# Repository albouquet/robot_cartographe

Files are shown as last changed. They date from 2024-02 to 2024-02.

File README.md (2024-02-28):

# Projet : Robot cartographe
## Par Alexandre Bouquet

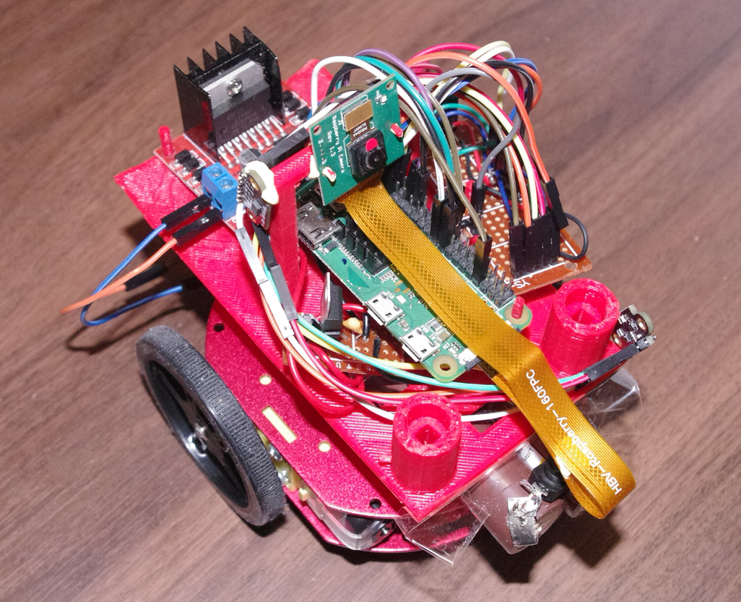
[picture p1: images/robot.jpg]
Robot Cartographe


## Introduction

L’objectif du projet est de créer un robot récupérant des informations télémétriques sur son environnement, afin d’en réaliser un mappage 2D de ce dernier.

Grâce à une connexion WIFI, le robot doit pouvoir envoyer un flux vidéo à l’utilisateur, recevoir les commandes de navigation de celui-ci, et transmettre des données télémétriques (+ coordonnées x,y du robot).

A coté de cela, un logiciel devra réaliser le plan 2D de l’environnement du robot, grâce aux données reçues.

## Partie I : Choix des composants

Je suis partie d’un support comportant deux motoréducteurs, deux roues et une bille centrale.

J’ai choisi une Raspberry pi zéro pour le contrôle central, pour plusieurs raisons :
* Développement rapide avec python
* Déjà équipée d’une caméra, du wifi et de GPIO
* De petite taille, faible consommation

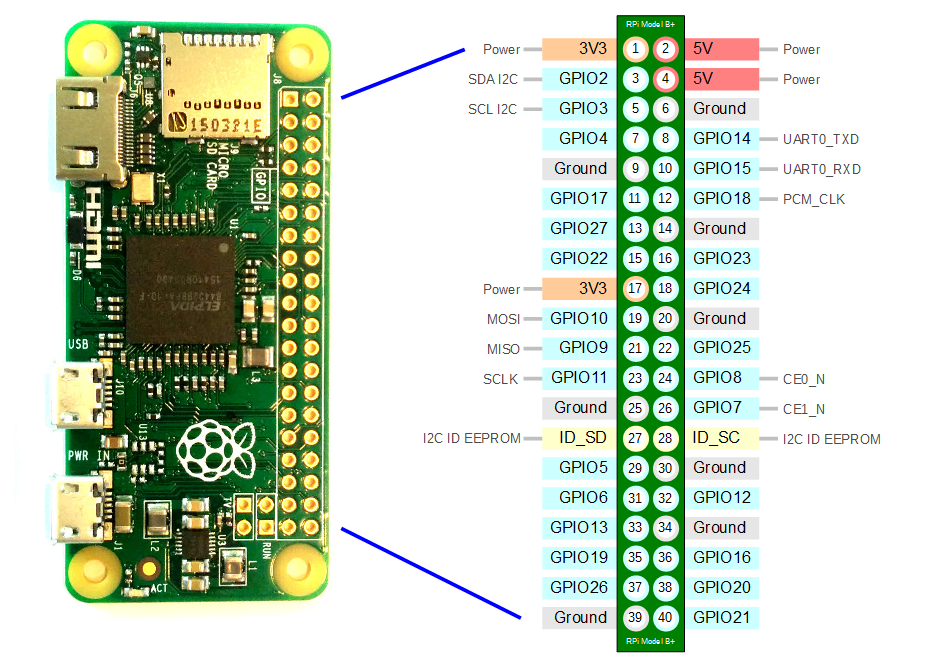
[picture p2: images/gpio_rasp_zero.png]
Figure 1: Raspberry pi zero


Deux capteurs télémétriques VL53L0X sont utilisés. La distance mesurée est de l’ordre du mètre.
En effet, ne sachant pas exactement la structure finale du projet, je suis finalement resté sur ce modèle.

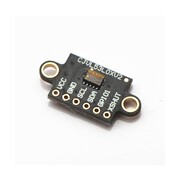
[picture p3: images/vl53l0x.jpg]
Figure 2: Capteur VL53L0X


Afin de contrôler les deux moteurs, j’utilise le L298N. Doté d’un pont en H et d’un régulateur 5v, il permet de piloter les moteurs d’avant en arrière pour chacun d’eux, grâce à des signaux PWM et de contrôles.

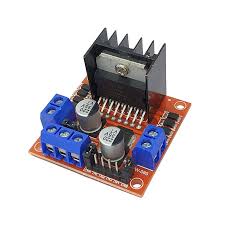
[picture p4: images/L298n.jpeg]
Figure 3: Module L298N


Deux batteries 18650 (pour un total de 8,4v) permettent d’alimenter la Raspberry pi et le L298N.

## Partie II : Alimentation

Comme dit précédemment, le L298N possède une sortie 5V. Je pensais l’utiliser pour alimenter la Pi lorsque je me suis rendu compte qu’elle pouvait délivrer moins de 500mA. 
Or, le démarrage de la Raspberry pi est consommateur. 
De plus, l’alimentation est bruitée lorsque les moteurs sont utilisés.

J’ai donc décidé de créer une alimentation stabilisée de 5V, alimentée par les batteries.
Pour cela, j’ai utilisé le régulateur 5V L7805CV, combiné avec deux condensateurs afin de filtrer la sortie.

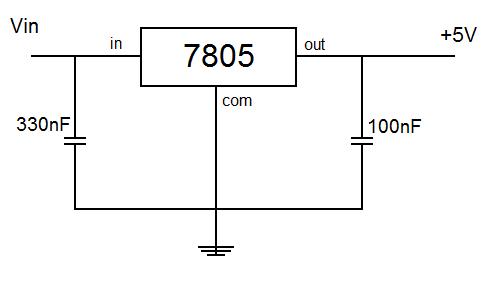
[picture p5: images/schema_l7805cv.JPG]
Figure 4: Schéma aliementation régulée à 5V


L’ensemble est soudé sur une carte à pastille :

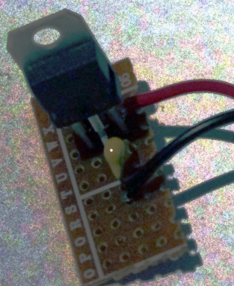
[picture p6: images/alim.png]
Figure 5: Régulateur 5V soudé sur plaque à pastille


## Partie III : Contrôle des Moteurs

Le L298N permet le contrôle de 2 moteurs grâce à :
* 2 signaux PWM pour l’alimentation
* 4 signaux de contrôles pour le sens de rotation

Ce module est directement alimenté par les batteries. La Raspberry pi fournie les 6 signaux nécessaires pour l’utilisation du module grâce à ses GPIO.

La tension moyenne nécessaire pour la rotation d’une roue est de 35 % de 8,4V donc environ 3V.

Les signaux PWM sont de type matériel sur la Pi, ce qui évite de consommer du temps processeur pour les générer.

## Partie IV : Contrôle des capteurs

Les capteurs télémétriques utilisés sont les VL53L0X.
Ils communiquent à travers un bus I2C (SDA, SCL). Par défaut, les deux ont l’adresse 0x29 une fois connectés au bus.
Pour la changer (et pouvoir identifier les deux), j’utilise la broche XSHUT afin d’activer les capteurs un par un (et effectuer le changement d’adresse).

Pour relier les deux capteurs au bus I2C de la Raspberry Pi, j’ai soudé un bus sur une plaque à pastille, afin de mettre en commun l’alimentation, le SDA et le SCL :

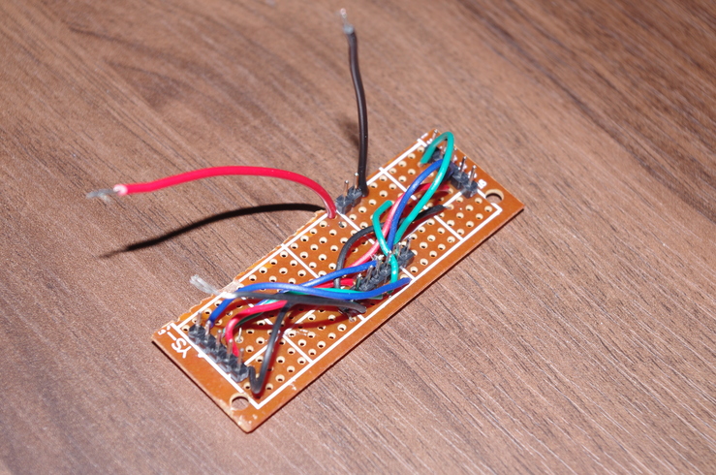
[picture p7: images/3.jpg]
Figure 6: Bus soudé pour relier les deux capteurs de distance au bus I2C


La bibliothèque python adafruit_vl53l0x permet un contrôle aisé des capteurs
(changement d’adresse + récupération distance).

Lorsque le capteur ne peut calculer la distance car celle-ci est trop grande (supérieur à 1.5 mètres), celui-ci renvoi 817 (plus de 8 mètres). C’est donc pris en compte lors de la réalisation du plan 2D.

## Partie V : Réalisation 3D

Afin de maintenir les composants en place sur le support, j’ai dessiné sous FreeCAD un deuxième support, et l’ai imprimé avec mon imprimante 3D :

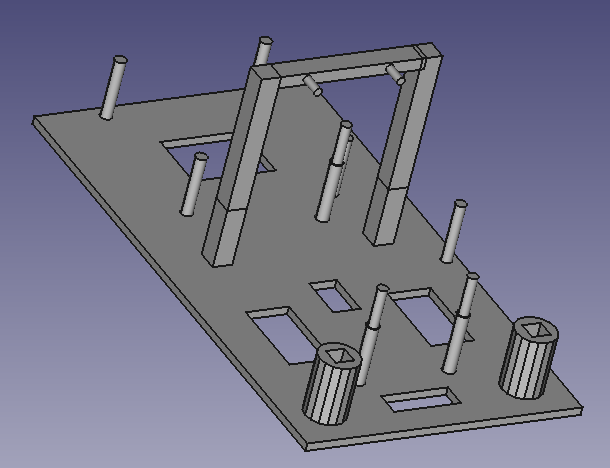
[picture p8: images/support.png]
Figure 6: Support


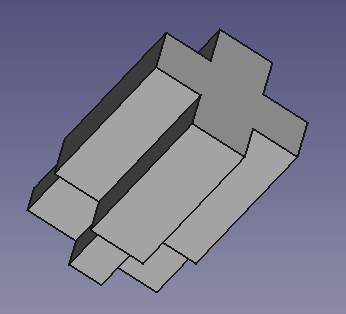
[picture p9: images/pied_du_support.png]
Figure 7: pied_Support

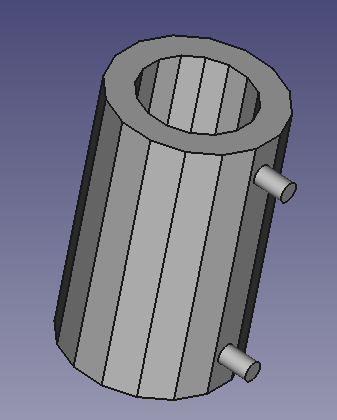
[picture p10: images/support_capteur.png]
Figure 8: Support_capteur


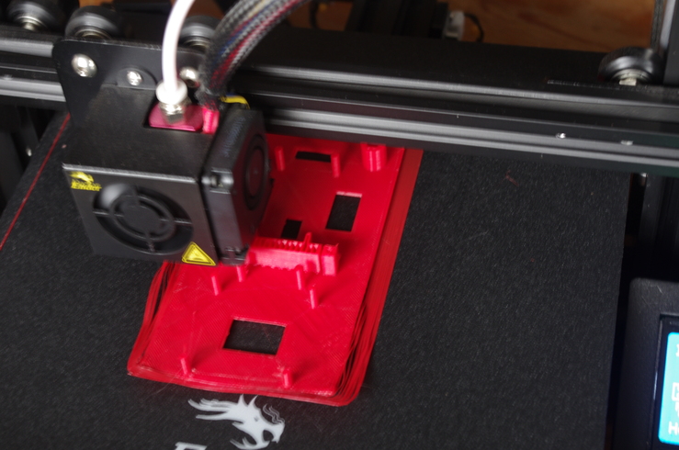
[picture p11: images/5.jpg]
Figure 9: Impre3D_1

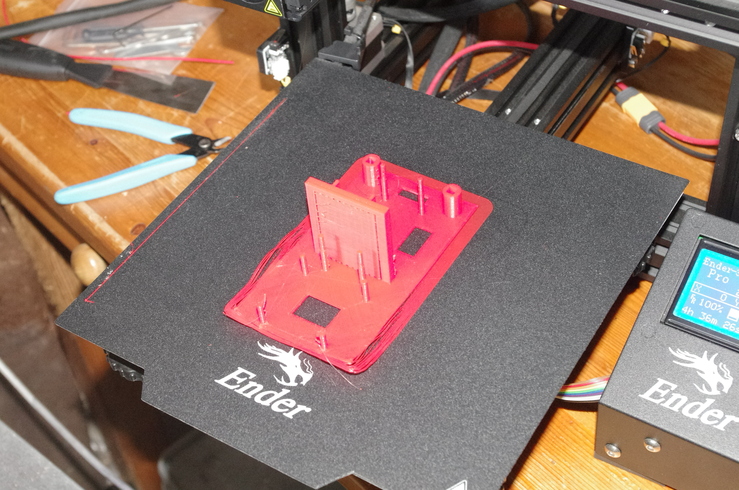
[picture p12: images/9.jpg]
Figure 10: Impre3D_2


## Partie VI : Fonctionnement du robot

Trois programmes python ont été réalisés : un pour la Raspberry pi (le robot), un pour l’ordinateur de l’utilisateur, un pour réaliser le mappage 2D avec le fichier de donnée.

Tout d’abord, la Raspberry pi se connecte à l’ordinateur de l’utilisateur.

Trois sockets sont utilisées :
* une pour l’envoi de la vidéo (type filelike)
* une pour l’envoie des données télémétriques et des coordonnées (x,y)
* une pour la réception des commandes de l’utilisateur

La vidéo et les données télémétriques sont stockées dans deux fichiers différents.

Si le robot effectue une rotation ou s’il avance, les coordonnées du robot (x et y) sont modifiées.

Par manque de temps, j’ai programmé des rotations de 90 degrés
uniquement. Cela simplifie les calculs de coordonnées du robot, et évite de
rajouter des erreurs de positionnement.

Lorsque le robot est en mode « avancer », les données des capteurs sont
transmises et les coordonnées s’adaptent toutes les 0,2 secondes.

Sur l’ordinateur de l’utilisateur, un terminal permet d’envoyer les
commandes, et récupérer la vidéo transmise par le robot, affichée grâce au
lecteur MPV.

La vidéo à un retard de plusieurs secondes par rapport à la réalité.
Le logiciel de mappage 2D dessine les liens entre tous les points renvoyés
par les capteurs. Il utilise la bibliothèque Matplotlib.

Schéma électrique final du projet :

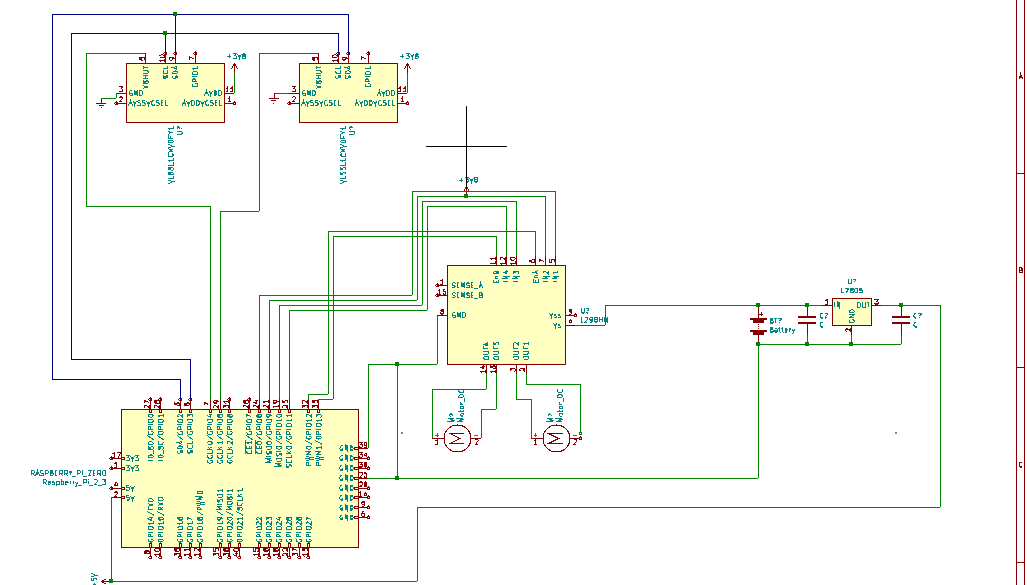
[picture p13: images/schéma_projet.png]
Figure 11: Schéma électrique du projet


## Partie VII : Tests

### Calibrage des capteurs VL53L0X

J’ai constaté que les capteurs ne renvoyaient pas la même valeur de distance pour une
même distance.

Par conséquent, j’ai réalisé une calibration des capteurs grâce à un plan fixe.
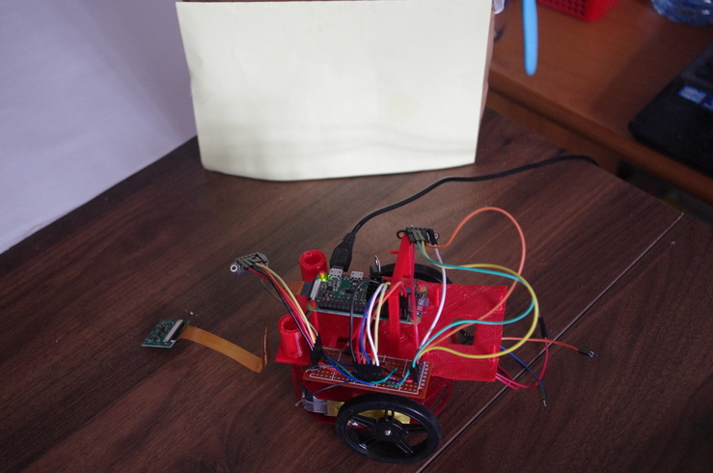
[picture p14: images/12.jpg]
Figure 12: Calibrage des capteurs de distance

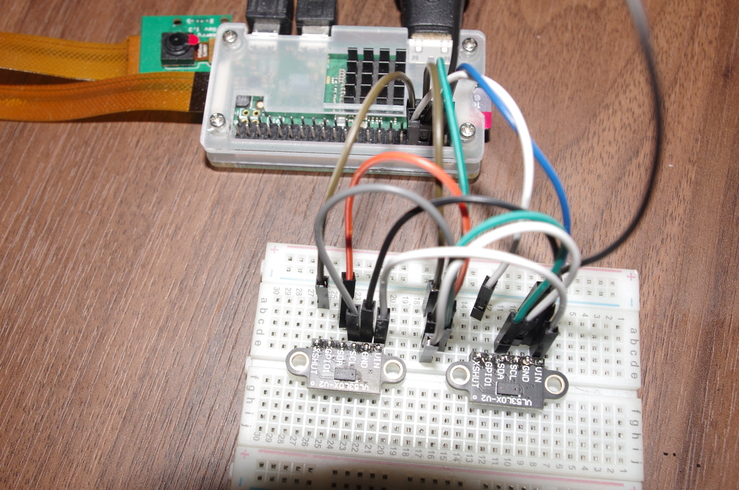
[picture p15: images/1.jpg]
Figure 13: Test capteurs de distance


### Vérification des signaux PWM pour les moteurs

Les signaux PWM sont générés par la Raspberry pi. Ils vont de 0 à 3.3V lorsque le
dutycycle est à 100 % :

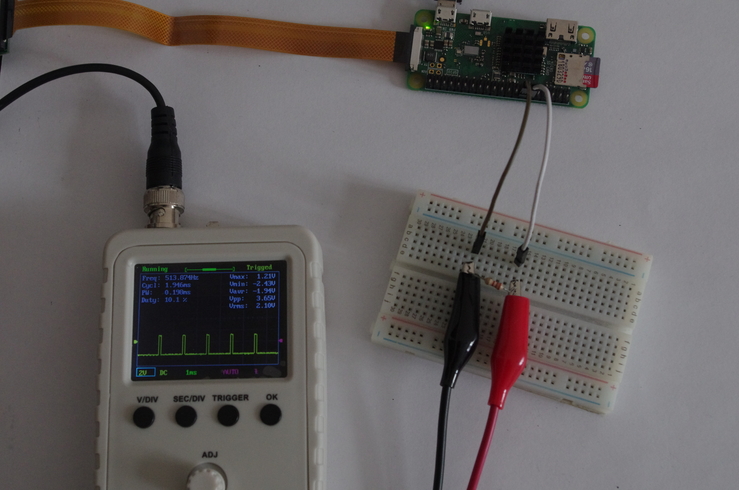
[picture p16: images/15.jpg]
Figure 14: Test PWM dutycycle à 10%


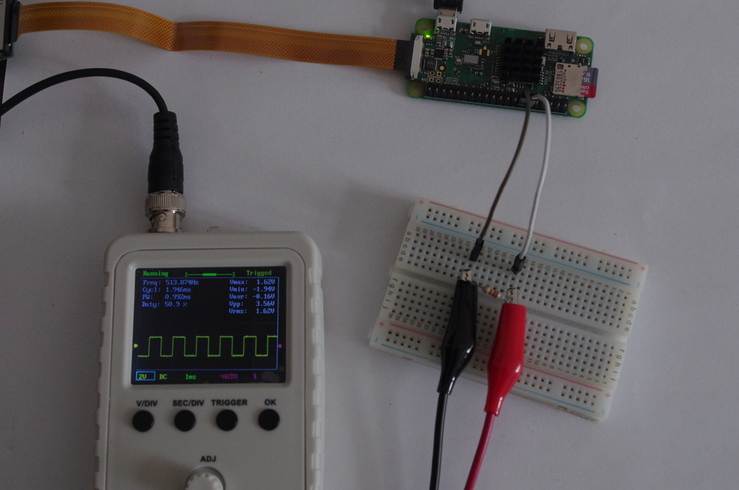
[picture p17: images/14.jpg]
Figure 15: Test PWM dutycycle à 50%


### Test complet du robot

J’ai réalisé le test de la totalité des fonctionnalités du robot sur une table plate.

Chacune a été testée :
* Connexion au réseau WIFI local
* Transmission/Réception des commandes de l’utilisateur
* Transmission/Réception du flux vidéo, données télémétrique, coordonnées du robot (x,y)
* Enregistrement dans un fichier la vidéo et dans un autre les données.
* Translation avant, rotation gauche/droite, arrêt

### Test sur parcours

J’ai vérifié la performance du robot sur un parcours intérieur, avec un sol avec des
rainures (sol non plat → voir la vidéo du projet). Le robot a réalisé les objectifs
attendus (transmission/réception vidéo, données, commandes).

Mais plusieurs problèmes ont été constatés :
* les roues du robot vibrent et ne permettent pas au robot de rester bien droit (perte de précision de positionnement du robot).
* L’engin en lui-même vibre beaucoup (désagréable sur la vidéo)
* Un sol qui n’est pas plat peut entraver le robot
* les rotations du robot sont très approximatives

Pour que le plan final soit parfait, il est nécessaire d’avoir les coordonnées de positon
du robot exacte et une fréquence d’envoi des données télémétriques assez grande.

VOIR video demo

### Modélisation 2D de l’environnement

Avec le programme réalisé nommé « mappage_2D », les coordonnées envoyées par
le robot ont pu être traitées afin de définir le plan de la zone d’évolution du robot :

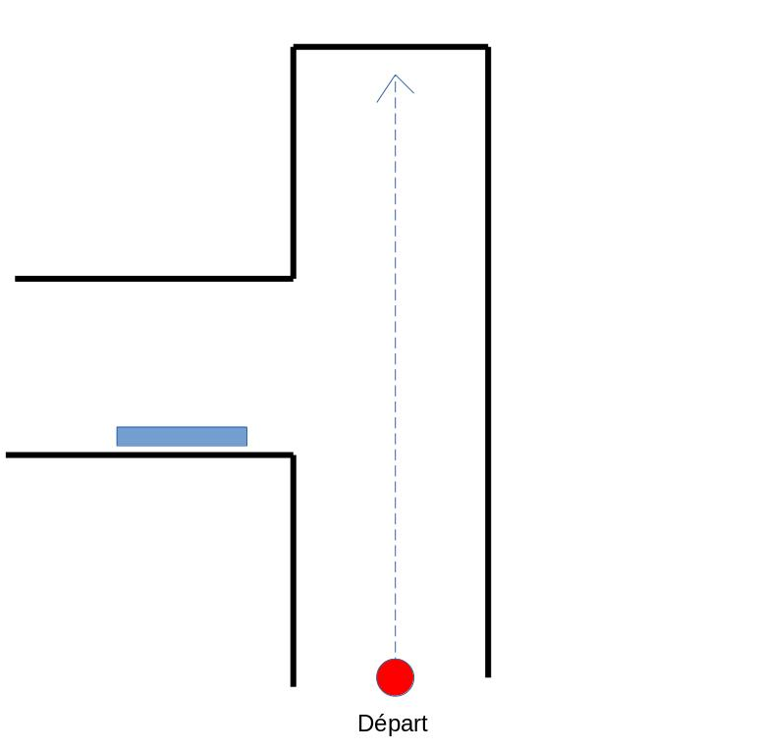
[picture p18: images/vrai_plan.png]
Figure 16: Vrai plan du terrain de test


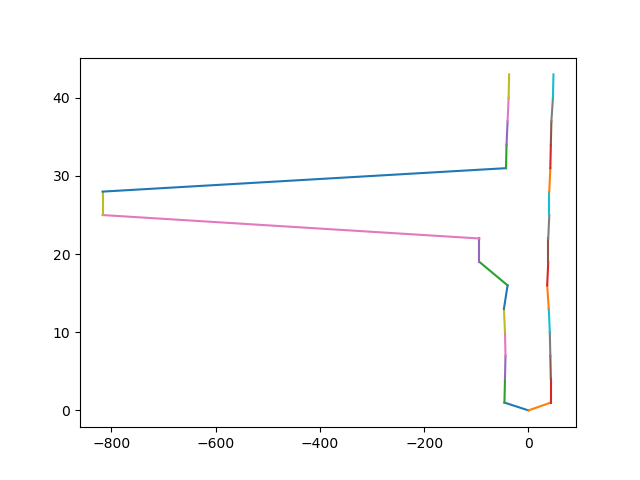
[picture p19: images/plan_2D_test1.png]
Figure 17: Plan 2D créé par le robot (conservation des points de vide)


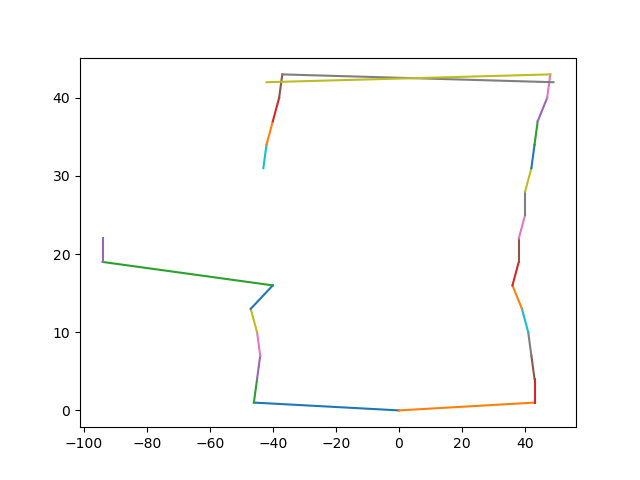
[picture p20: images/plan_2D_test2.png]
Figure 18: Plan 2D créé par le robot (sans point de vide)


## Partie VIII : Points d’améliorations

La structure du robot doit être améliorée afin d’éviter tout basculement et vibration
du robot.
De plus, la façon de calculer la position du robot (en fonction de la rotation et du temps de translation) est à changer par une technique plus précise.
Enfin, je n’ai pas eu le temps de réaliser le traitement des images reçues pour augmenter la précision de la modélisation de l’environnement.

## Conclusion
Ce projet a demandé des compétences dans différents domaine, comme la programmation python, le réseau, Linux, l’électronique et la CAO.

Le prototype du robot cartographe réalise les objectifs attendus :
* Réception des commandes
* Transmission vidéo, données télémétrique
* Mappage 2D proche du plan réel du terrain

Mais il comporte un certains nombres de points à améliorer, de la structure non fixe, à la précision du mappage 2D, en passant par la maîtrise de l’angle de rotation de l’engin.

### A savoir

Le programme à placer sur la Raspberry pi est prog_pi.py

Le programme à placer sur l'ordinateur de l'utilisateur est prog_utilisateur.py

Le programme pour mapper un plan 2D gràce à un fichier de données est mappage_2D.py

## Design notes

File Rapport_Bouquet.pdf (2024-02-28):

# Projet Robot cartographe

### Alexandre Bouquet

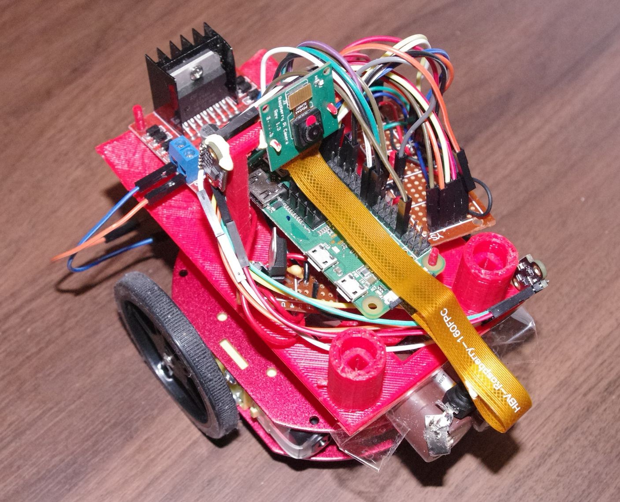
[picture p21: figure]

Sommaire

## Introduction

L’objectif du projet est de créer un robot récupérant des informations télémétriques sur son environnement, afin d’en réaliser un mappage 2D de ce dernier.
Grâce à une connexion WIFI, le robot doit pouvoir envoyer un flux vidéo à l’utilisateur, recevoir les commandes de navigation de celui-ci, et transmettre des données télémétriques (+ coordonnées x,y du robot).
A coté de cela, un logiciel devra réaliser le plan 2D de l’environnement du robot, grâce aux données reçues.

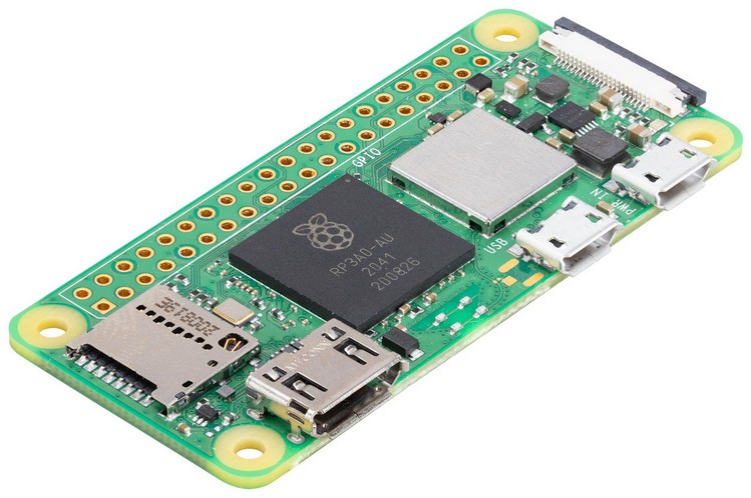
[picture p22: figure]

Figure 1: Raspberry pi zero

## Partie I : Choix des composants

Je suis partie d’un support comportant deux motoréducteurs, deux roues et une bille centrale.

J’ai choisi une Raspberry pi zéro pour le contrôle central, pour plusieurs raisons :
- Développement rapide avec python
- Déjà équipée d’une caméra, du wifi et de GPIO
- De petite taille, faible consommation

Deux capteurs télémétriques VL53L0X sont utilisés. La distance mesurée est de l’ordre du mètre. En effet, ne sachant pas exactement la structure finale du projet, je suis finalement resté sur ce modèle.

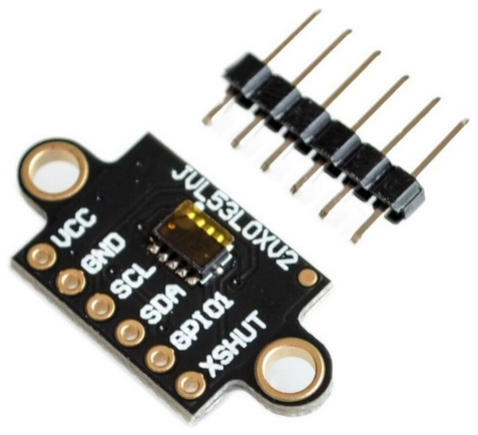
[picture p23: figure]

Afin de contrôler les deux moteurs, j’utilise le L298N. Doté d’un pont en H et d’un régulateur 5v, il permet de piloter les moteurs d’avant en arrière pour chacun d’eux, grâce à des signaux PWM et de contrôles.

Deux batteries 18650 (pour un total de 8,4v) permettent d’alimenter la Raspberry pi et le L298N.

Figure 2: Capteur VL53L0X

Figure 3: Module L298N

## Partie II : Alimentation

Comme dit précédemment, le L298N possède une sortie 5V. Je pensais l’utiliser pour alimenter la Pi lorsque je me suis rendu compte qu’elle pouvait délivrer moins de 500 mA. Or, le démarrage de la Raspberry pi est consommateur. De plus, l’alimentation est bruitée lorsque les moteurs sont utilisés.
J’ai donc décidé de créer une alimentation stabilisée de 5V, alimentée par les batteries. Pour cela, j’ai utilisé le régulateur 5V L7805CV, combiné avec deux condensateurs afin de filtrer la sortie.

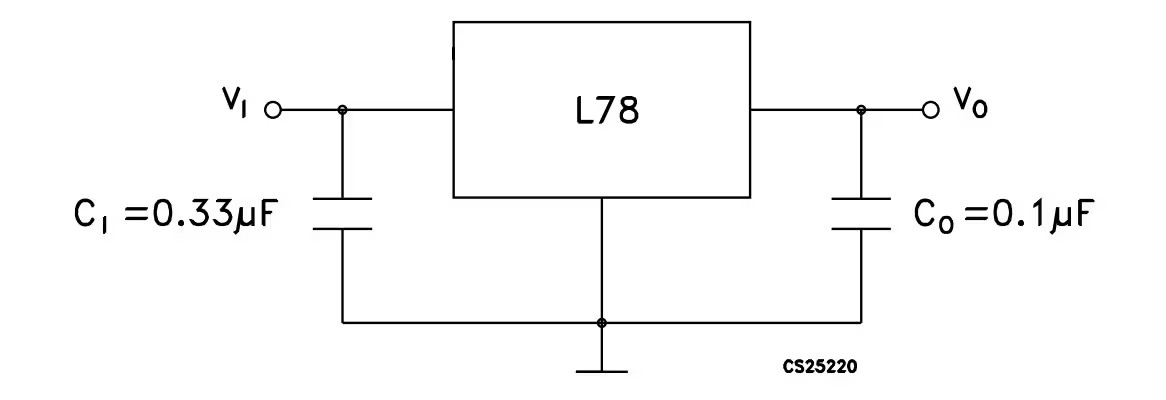
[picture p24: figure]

L’ensemble est soudé sur une carte à pastille :

Figure 4: Schéma aliementation régulée à 5V

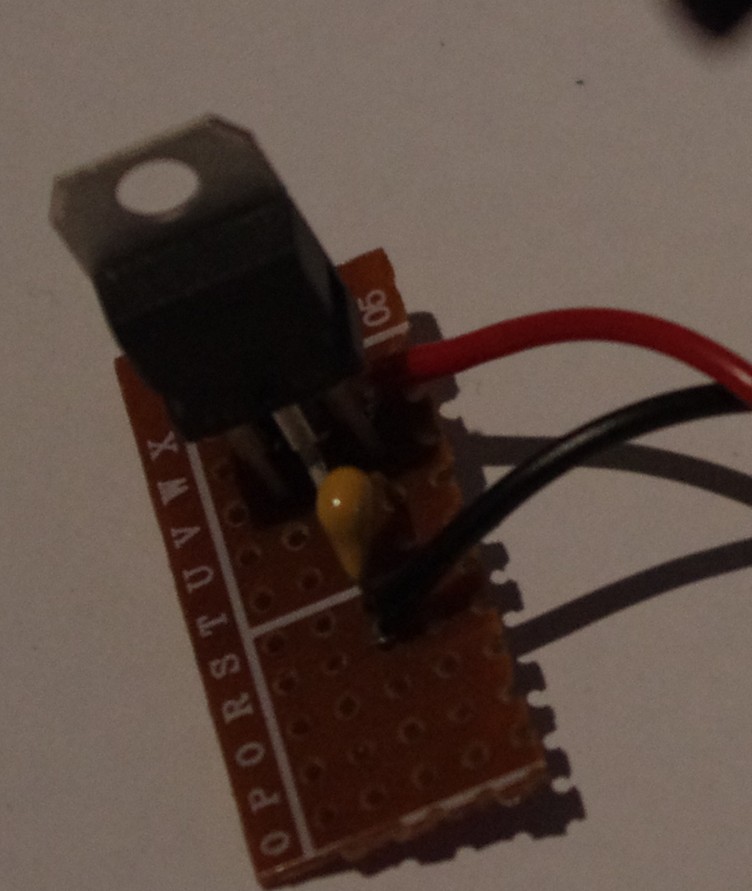
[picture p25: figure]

Figure 5: Régulateur 5V soudé sur plaque à pastille

## Partie III : Contrôle des Moteurs

Le L298N permet le contrôle de 2 moteurs grâce à :
- 2 signaux PWM pour l’alimentation
- 4 signaux de contrôles pour le sens de rotation

Ce module est directement alimenté par les batteries. La Raspberry pi fournie les 6 signaux nécessaires pour l’utilisation du module grâce à ses GPIO.
La tension moyenne nécessaire pour la rotation d’une roue est de 35 % de 8,4V donc environ 3V.
Les signaux PWM sont de type matériel sur la Pi, ce qui évite de consommer du temps processeur pour les générer.

## Partie IV : Contrôle des capteurs

Les capteurs télémétriques utilisés sont les VL53L0X.
Ils communiquent à travers un bus I2C (SDA, SCL). Par défaut, les deux ont l’adresse 0x29 une fois connectés au bus. Pour la changer (et pouvoir identifier les deux), j’utilise la broche XSHUT afin d’activer les capteurs un par un (et effectuer le changement d’adresse).

Pour relier les deux capteurs au bus I2C de la Raspberry Pi, j’ai soudé un bus sur une plaque à pastille, afin de mettre en commun l’alimentation, le SDA et le SCL :

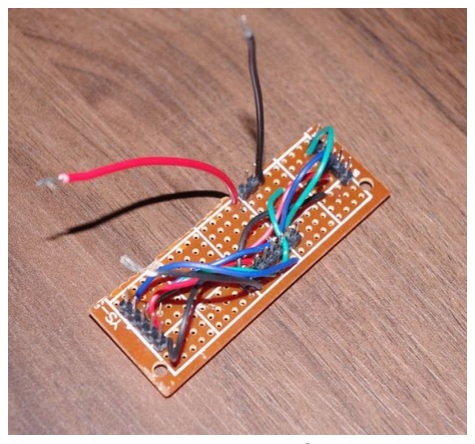
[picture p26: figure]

La bibliothèque python adafruit_vl53l0x permet un contrôle aisé des capteurs (changement d’adresse + récupération distance).

Lorsque le capteur ne peut calculer la distance car celle-ci est trop grande (supérieur à 1.5 mètres), celui-ci renvoi 817 (plus de 8 mètres). C’est donc pris en compte lors de la réalisation du plan 2D.

Figure 6: Bus soudé pour
relier les deux capteurs de distance au bus I2C

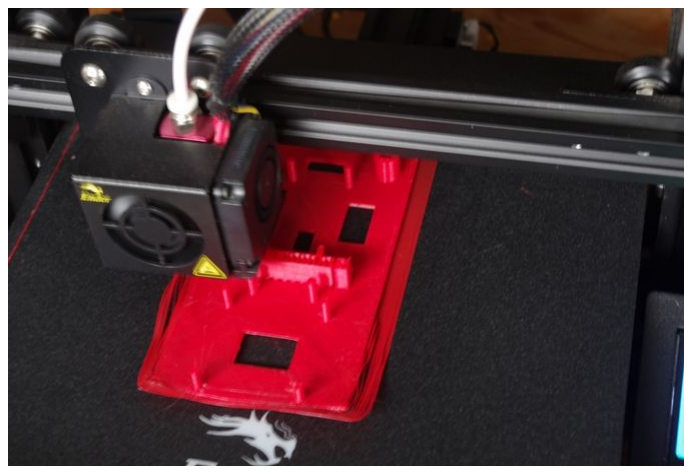
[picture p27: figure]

Figure 8: Impression du support

## Partie V : Réalisation 3D

Afin de maintenir les composants en place sur le support, j’ai dessiné sous FreeCAD un deuxième support, et l’ai imprimé avec mon imprimante 3D :


Figure 7: Support dessiné sur FreeCAD

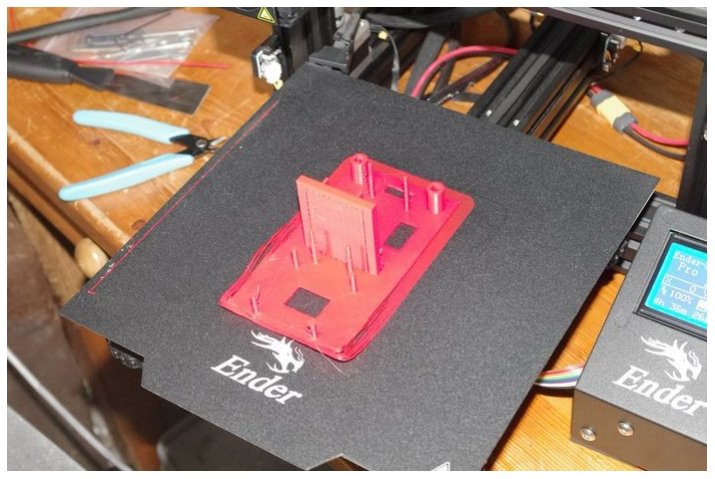
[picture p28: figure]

Figure 9: Fin de l'impression

## Partie VI : Fonctionnement du robot

Trois programmes python ont été réalisés : un pour la Raspberry pi (le robot), un pour l’ordinateur de l’utilisateur, un pour réaliser le mappage 2D avec le fichier de donnée.
Tout d’abord, la Raspberry pi se connecte à l’ordinateur de l’utilisateur. Trois sockets sont utilisées :
- une pour l’envoi de la vidéo (type filelike)
- une pour l’envoie des données télémétriques et des coordonnées (x,y)
- une pour la réception des commandes de l’utilisateur
La vidéo et les données télémétriques sont stockées dans deux fichiers différents.

Si le robot effectue une rotation ou s’il avance, les coordonnées du robot (x et y) sont modifiées.

Par manque de temps, j’ai programmé des rotations de 90 degrés uniquement. Cela simplifie les calculs de coordonnées du robot, et évite de rajouter des erreurs de positionnement.

Lorsque le robot est en mode « avancer », les données des capteurs sont transmises et les coordonnées s’adaptent toutes les 0,2 secondes.

Sur l’ordinateur de l’utilisateur, un terminal permet d’envoyer les commandes, et récupérer la vidéo transmise par le robot, affichée grâce au lecteur MPV.

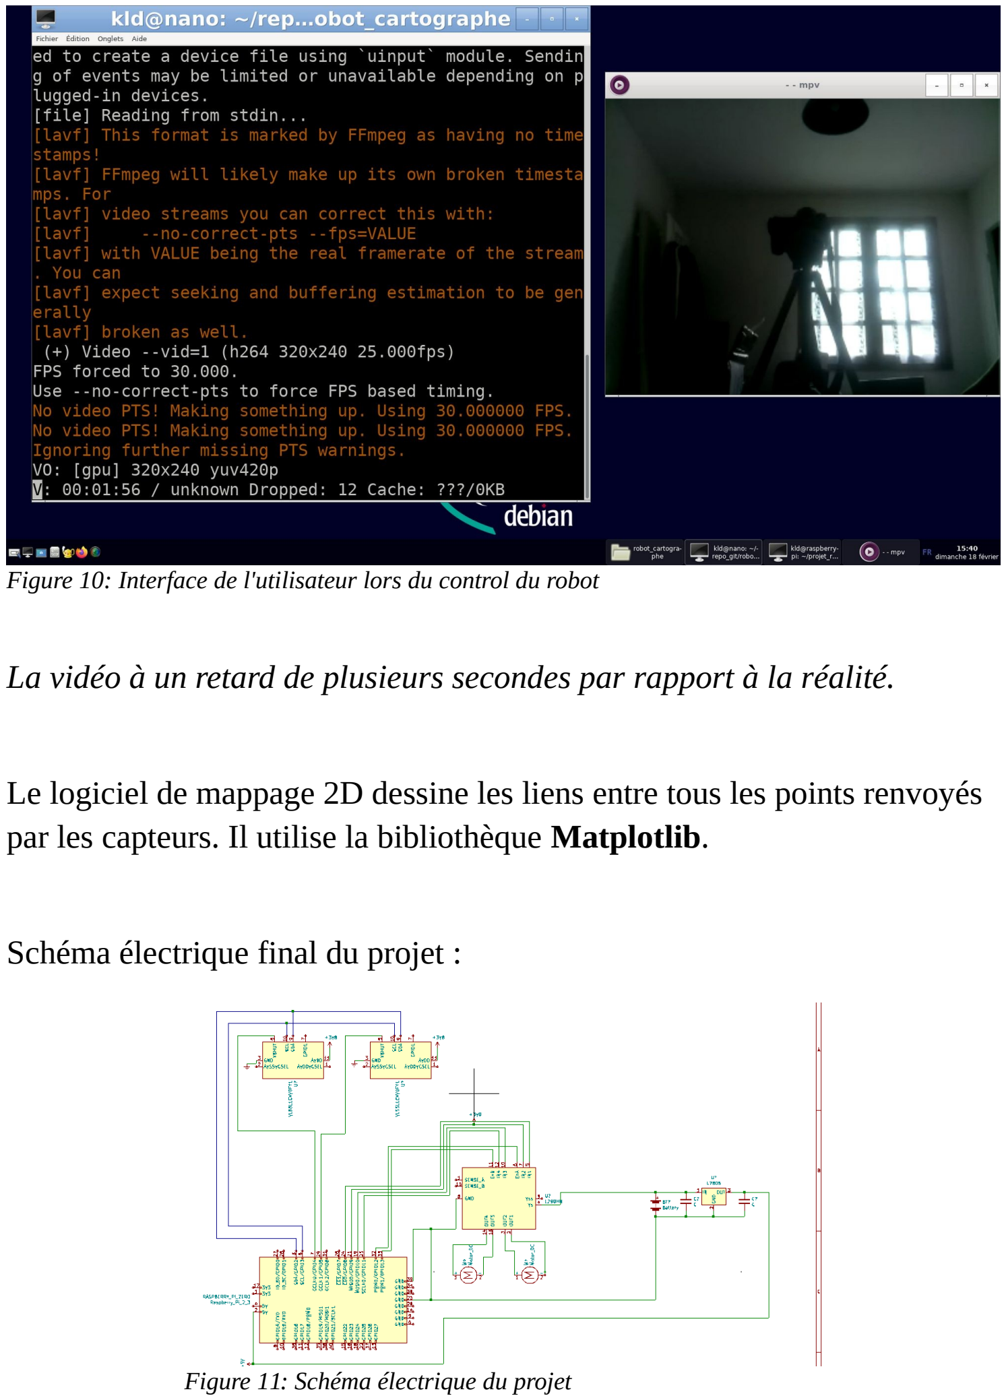
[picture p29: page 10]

La vidéo à un retard de plusieurs secondes par rapport à la réalité.

Le logiciel de mappage 2D dessine les liens entre tous les points renvoyés par les capteurs. Il utilise la bibliothèque Matplotlib.

Schéma électrique final du projet :

Figure 10: Interface de l'utilisateur lors du control du robot

Figure 11: Schéma électrique du projet

## Partie VII : Tests

### 1. Calibrage des capteurs VL53L0X

J’ai constaté que les capteurs ne renvoyaient pas la même valeur de distance pour une même distance.
Par conséquent, j’ai réalisé une calibration des capteurs grâce à un plan fixe.

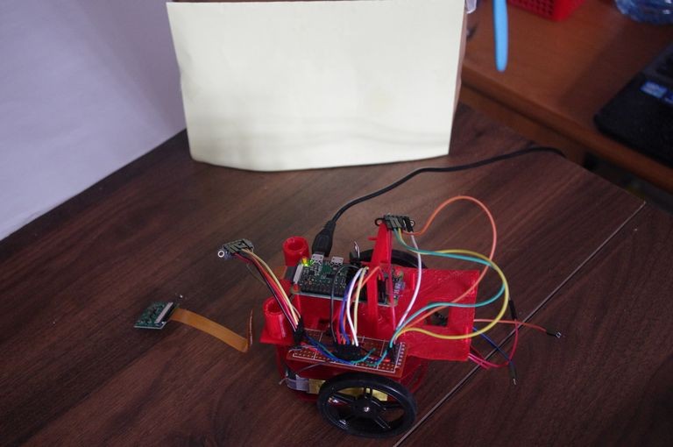
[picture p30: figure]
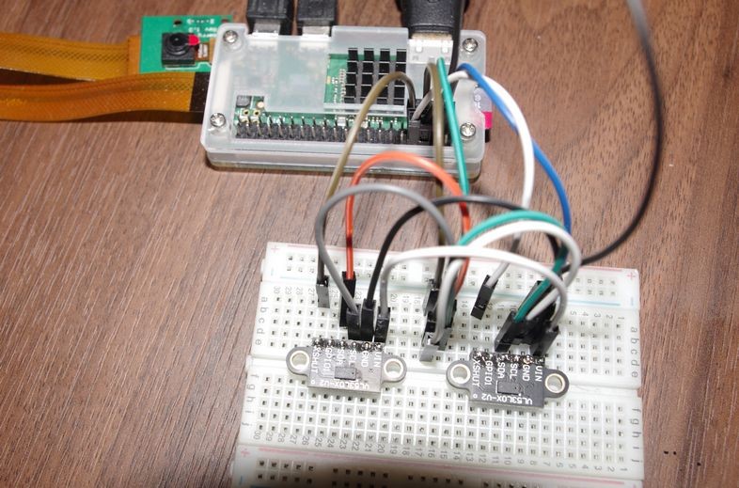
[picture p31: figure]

### 2. Vérification des signaux PWM pour les moteurs

Les signaux PWM sont générés par la Raspberry pi. Ils vont de 0 à 3.3V lorsque le dutycycle est à 100 % :

Figure 12: Calibrage des capteurs de distance

Figure 13: Test capteurs de distance

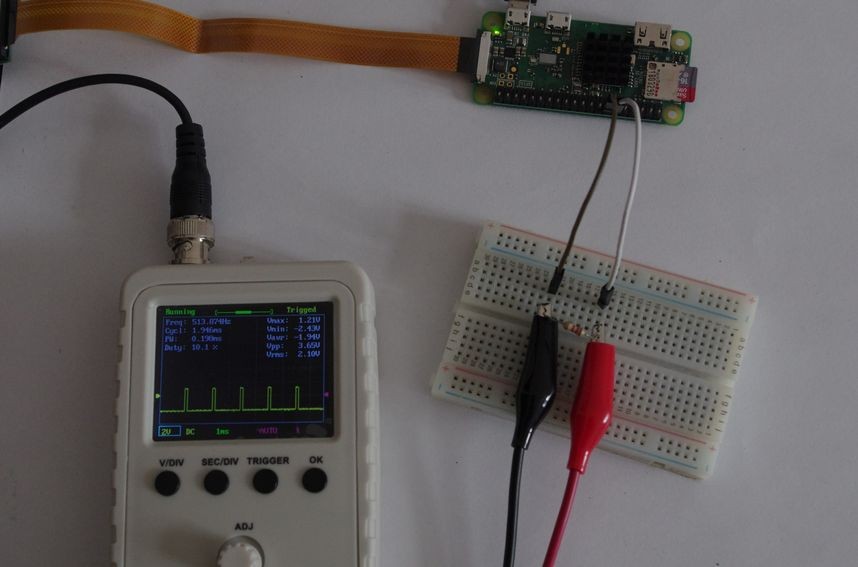
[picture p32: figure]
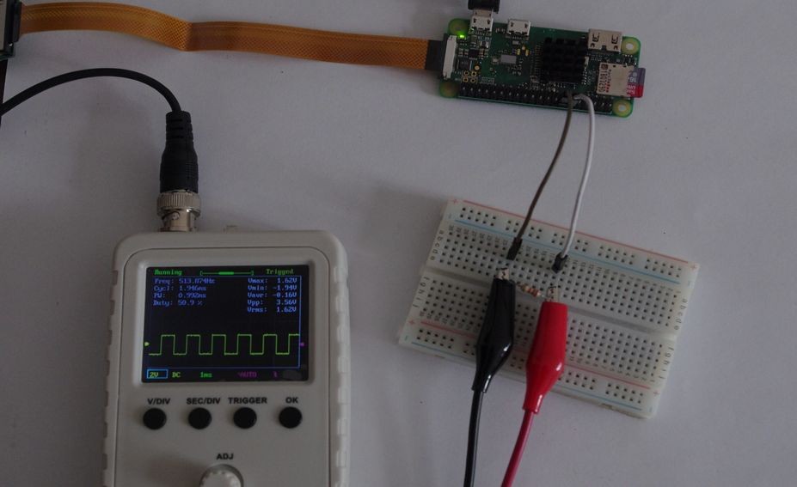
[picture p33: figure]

Figure 15: Test PWM dutycycle à 50% | Figure 14: Test PWM dutycycle à 10%

### 3. Test complet du robot

J’ai réalisé le test de la totalité des fonctionnalités du robot sur une table plate. Chacune a été testée :
- Connexion au réseau WIFI local
- Transmission/Réception des commandes de l’utilisateur
- Transmission/Réception du flux vidéo, données télémétrique, coordonnées du robot (x,y)
- Enregistrement dans un fichier la vidéo et dans un autre les données.
- Translation avant, rotation gauche/droite, arrêt

### 4. Test sur parcours

J’ai vérifié la performance du robot sur un parcours intérieur, avec un sol avec des rainures (sol non plat → voir la vidéo du projet). Le robot a réalisé les objectifs attendus (transmission/réception vidéo, données, commandes).
Mais plusieurs problèmes ont été constatés :
- les roues du robot vibrent et ne permettent pas au robot de rester bien droit (perte de précision de positionnement du robot).
- L’engin en lui-même vibre beaucoup (désagréable sur la vidéo)
- Un sol qui n’est pas plat peut entraver le robot
- les rotations du robot sont très approximatives

Pour que le plan final soit parfait, il est nécessaire d’avoir les coordonnées de positon du robot exacte et une fréquence d’envoi des données télémétriques assez grande.

### 5. Modélisation 2D de l’environnement

Avec le programme réalisé nommé « mappage_2D », les coordonnées envoyées par le robot ont pu être traitées afin de définir le plan de la zone d’évolution du robot :

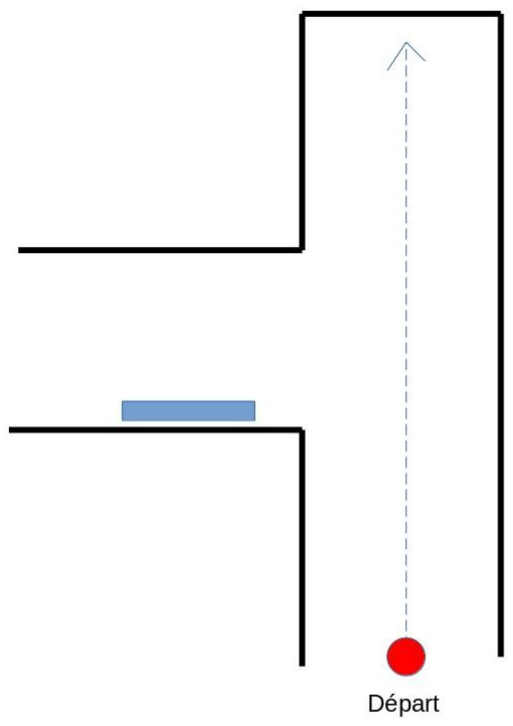
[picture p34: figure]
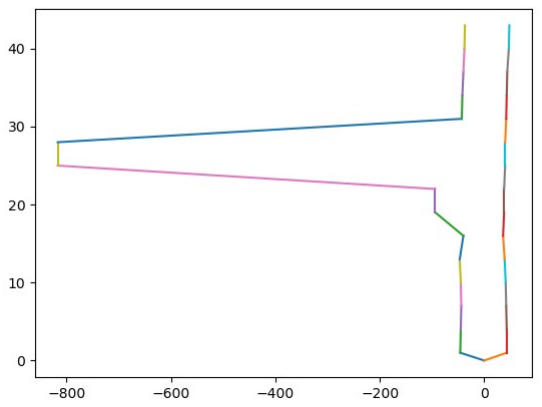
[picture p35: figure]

Figure 17: Plan 2D créé par le robot (conservation des points de vide)

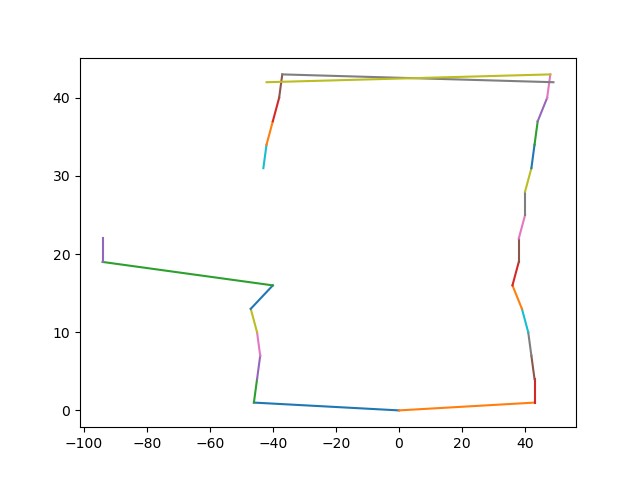
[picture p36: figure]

Figure 18: Plan 2D créé par le robot (sans point de vide)

Figure 16: Vrai plan du terrain de test

## Partie VIII : Points d’améliorations

La structure du robot doit être améliorée afin d’éviter tout basculement et vibration du robot.
De plus, la façon de calculer la position du robot (en fonction de la rotation et du temps de translation) est à changer par une technique plus précise.
Enfin, je n’ai pas eu le temps de réaliser le traitement des images reçues pour augmenter la précision de la modélisation de l’environnement.

## Conclusion

Ce projet a demandé des compétences dans différents domaine, comme la programmation python, le réseau, Linux, l’électronique et la CAO.

Le prototype du robot cartographe réalise les objectifs attendus :
- Réception des commandes
- Transmission vidéo, données télémétrique
- Mappage 2D proche du plan réel du terrain

Mais il comporte un certains nombres de points à améliorer, de la structure non fixe, à la précision du mappage 2D, en passant par la maîtrise de l’angle de rotation de l’engin.

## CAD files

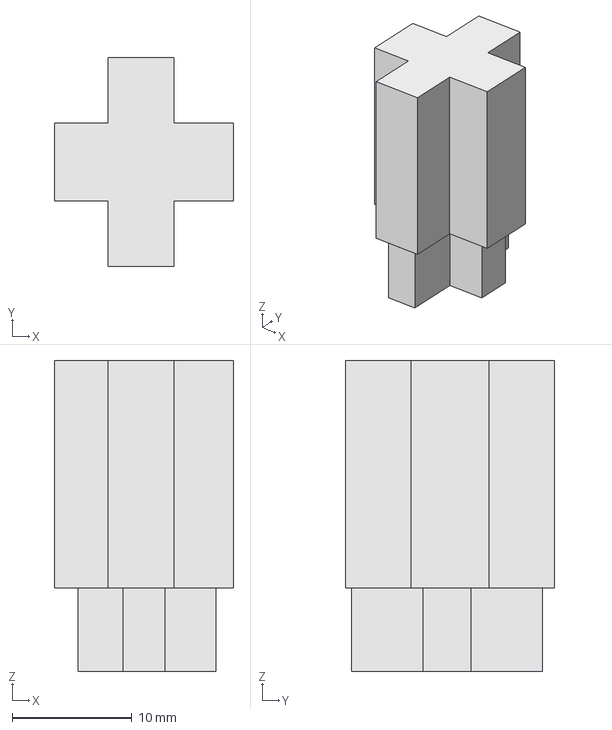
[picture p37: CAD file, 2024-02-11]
CAO/pieds-support.FCStd
15.0 x 17.5 x 26.0 mm

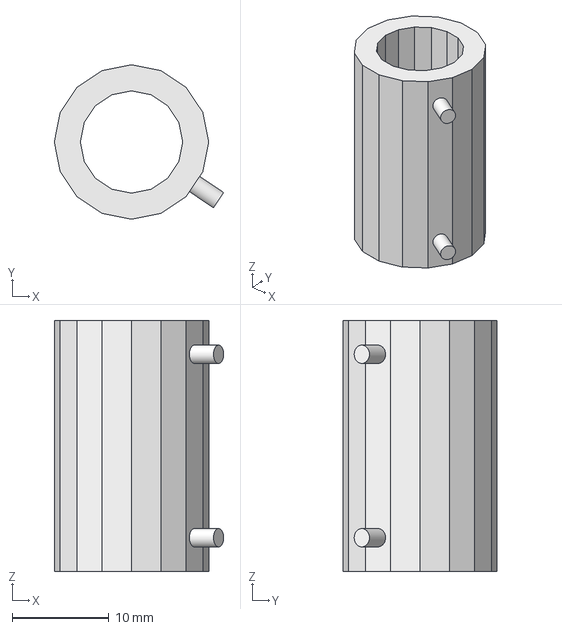
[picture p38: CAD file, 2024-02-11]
CAO/support_capteur.FCStd
17.5 x 16.0 x 26.0 mm

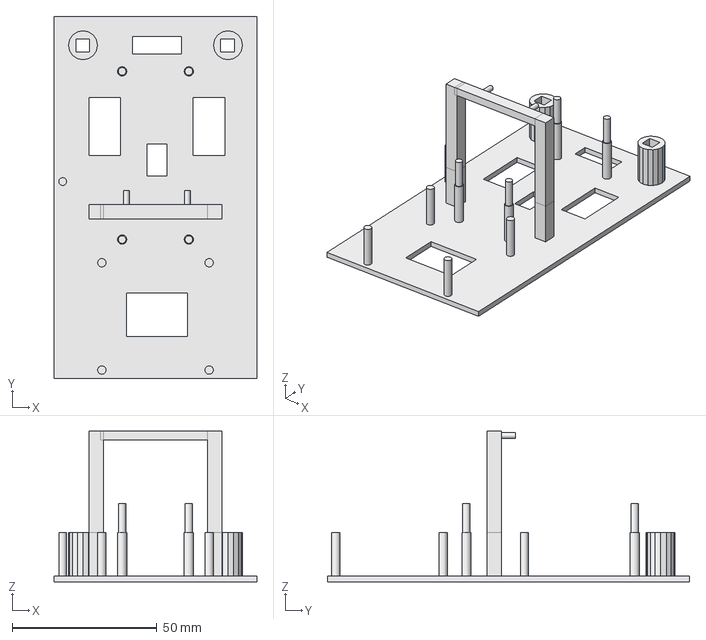
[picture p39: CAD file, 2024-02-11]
CAO/support_robot.FCStd
70.0 x 125.0 x 52.0 mm

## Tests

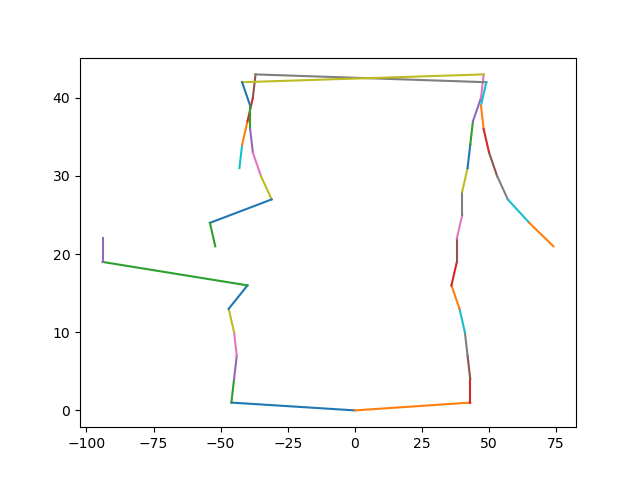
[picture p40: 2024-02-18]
TESTS/plan_2D_test3.png

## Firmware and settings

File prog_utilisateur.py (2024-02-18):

"""
Ce programme permet le controle du robot :
	- reception des données des capteurs de distance
	- reception du flux video du robot
	- envoie de commande au robot

Trois sockets sont ouvertes pour recupérer et envoyer ces données.

Le robot peut avancer ou effectuer une rotation à droite/gauche de 20°.
La barre d'espace permet de stopper le robot et e de l'eteindre.
"""
import socket
import cv2 as cv
import numpy as np
import pickle as pk
import subprocess
import keyboard
import threading
import time

#########	INITIALISATION socket capteur
socket_capt=socket.socket(socket.AF_INET,socket.SOCK_STREAM)
socket_capt.bind(('192.168.1.18',9322))
socket_capt.listen(1)
conn_capt = socket_capt.accept()[0]
#########	FIN initialisation socket capteur


######### 	INITIALISATION socket video
socket_vid=socket.socket(socket.AF_INET,socket.SOCK_STREAM)
socket_vid.bind(('192.168.1.18',9323))
socket_vid.listen(1)
conn_vid = socket_vid.accept()[0].makefile('rb')
fichier_video=open("video.h264", "wb")
######### 	FIN initialisation socket video

######### 	INITIALISATION socket commande
socket_cmd=socket.socket(socket.AF_INET,socket.SOCK_STREAM)
socket_cmd.bind(('192.168.1.18',9324))
socket_cmd.listen(1)
conn_cmd = socket_cmd.accept()[0]
######### 	FIN initialisation socket commande


def recup_capt():
	######### 	RECUPERATION des données des capteurs + coordonnées robot
	fichier_capt=open("data_capt.txt", "w")
	
	while True:
			chaine=""
			data = conn_capt.recv(256)
			if not data:
				break
			chaine=chaine+data.decode("UTF-8")
			fichier_capt.write(chaine+"\n")
			
	print(chaine)
	fichier_capt.close()
	conn_capt.close()
	######### 	FIN recuperation des données des capteurs + coordonnées robot


def recup_vid():
	#########	RECUPERATION du flux video
	try:
		while True:
			data = conn_vid.read(1024)
			if not data:
				break
			player.stdin.write(data)
			fichier_video.write(data)
	finally:
		fichier_video.close()
		conn_vid.close()
		socket_vid.close()
		player.terminate()
	#########	FIN recuperation du flux video








#########	LANCEMENT des threads (video + données capteurs)
thread_video=threading.Thread(target=recup_vid, args=())
thread_video.start()
thread_capt=threading.Thread(target=recup_capt, args=())
thread_capt.start()
#########	FIN lancement des threads (video + données capteurs)

######### 	DEMARRAGE du lecteur video mpv
cmdline = ['mpv','--fps=30','--cache=yes','-']
player = subprocess.Popen(cmdline, stdin=subprocess.PIPE)
######### 	FIN demarrage du lecteur video mpv



######### ENVOI des touches de controle

while True:

	#récupération de la touche:
	event=keyboard.read_key()
	
	#traitement de la touche:
	if event == "d":
			conn_cmd.send(b'd')
	elif event == "z":
			conn_cmd.send(b'z')
	elif event == "q":
			conn_cmd.send(b'q')
	elif event == "a":
			conn_cmd.send(b'a')
	elif event == "p":
			conn_cmd.send(b'p')
			conn_cmd.close()
			conn_vid.close()
			conn_capt.close()
			#thread_capt.stop()
			#thread_video.stop()
			break
	time.sleep(1)

######### FIN envoi des touches de controle

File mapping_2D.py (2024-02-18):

# Ce programme permet de réaliser un plan 2D grace au données d'un fichier en entré.
# Ce fichier contient 4 données par lignes, séparées par des espaces :
#	 distance_gauche distance_droite x y

import matplotlib.pyplot as plt
import numpy as np
import time


# Fonction de création du plan 2D
def map_2D(lines):
	global ax
	
	line1= [0,0,0,0]
	
	# Point à gauche du robot
	p1_temp_prec=[0,0]
	# Point à droite du robot
	p2_temp_prec=[0,0]
	
	for line2 in lines:
	
		if line2[2] != line1[2]:
			# x a changé
			if line2[2] < line1[2]:
				p1_temp=[ line2[2] , line2[3]-line2[0] ]
				p2_temp=[ line2[2] , line2[3]+line2[1] ]
			else :
				p1_temp=[ line2[2] , line2[3]+line2[0] ]
				p2_temp=[ line2[2] , line2[3]-line2[1] ]
		else :
			# y a changé
			if line2[3] < line1[3] :
				p1_temp=[ line2[2]+line2[0] , line2[3] ]
				p2_temp=[ line2[2]-line2[1] , line2[3] ]
			else :
				p1_temp=[ line2[2]-line2[0] , line2[3] ]
				p2_temp=[ line2[2]+line2[1] , line2[3] ]

		# Gestion des distances à 817 (distance inconnue car trop grande donc ne pas faire de lien entre les points)
		#if (abs(p1_temp_prec[0]) < 200 and abs(p1_temp[0]) < 200) :
		#	if (abs(p1_temp_prec[1]) < 200 and abs(p1_temp[1]) < 200) :
		ax.plot([p1_temp_prec[0],p1_temp[0]], [p1_temp_prec[1],p1_temp[1]])
		#if (abs(p2_temp_prec[0]) < 200 and abs(p2_temp[0]) < 200) :
		#	if (abs(p1_temp_prec[1]) < 200 and abs(p1_temp[1]) < 200) :
		ax.plot([p2_temp_prec[0],p2_temp[0]], [p2_temp_prec[1],p2_temp[1]])
		
		line1=line2
		p1_temp_prec=p1_temp
		p2_temp_prec=p2_temp

		plt.pause(0.4)





# Création du corps du plan
fig = plt.figure()
ax = plt.axes()

# Lecture et modification du fichier de données
with open("data_capt_111_125.txt") as temp_f:
	datafile = temp_f.readlines()
	
	for i in range(0,len(datafile)):
		# Symbole de fin de ligne supprimé
		datafile[i] = datafile[i].replace("\n", "")
		# Chaque nombre est séparé par un espace (symbole de séparation des nombres)
		datafile[i]=datafile[i].split(" ")
		# Les nombres sont en "string" donc je les retype intier
		datafile[i][:] = list(map(int, datafile[i]))
	
	map_2D(datafile)


# Affichage plan 2D
plt.show()

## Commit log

2023-11-12 Ajout du fichier de controle à distance du robot
2023-12-03 Test des capteurs + moteurs + schéma kicad
    Test des capteurs vl53l0x avec l'API adafruit
    Test des moteurs du robot avec PWM hardware
    Réalisation du schéma électronique
    [schema_robot_carto.sch]
2023-12-17 Reorganisation du projet Ajout du test de la video (transmission, reception par socket)
2023-12-17 Ajout repertoires
    [schema_robot_carto.kicad_pcb, schema_robot_carto.sch]
2024-01-01 Test de l'envoi/reception des données télémetrique / video et du control des moteurs
    [schema_robot_carto.sch]
2024-01-01 Modif du readme
    [schema_robot_carto.sch]
2024-01-01 Test ensemble de la video et des capteurs
2024-01-06 Ajout support robot CAO
    [pieds-support-Body.stl, support_robot-Body.stl]
2024-01-09 mise à jour des schémas et README
    [bus_i2c_alim.kicad_pcb, bus_i2c_alim.sch, schema_robot_carto.sch]
2024-01-15 Ajout video + fichiers
    [pieds-support-Body.step, support_robot-Body.step]
2024-01-21 Nouveau support CAO
    [support_robot-Body.stl]
2024-02-11 Assemblage et Ajout alimentation externe
    [pieds-support-Body.step, pieds-support-Body.stl, pieds-support.FCStd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]
2024-02-20 Dernier commit
    [bus_i2c_alim.kicad_pcb, bus_i2c_alim.sch, schema_robot_carto.kicad_pcb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]
2025-08-14 Epuration des videos
